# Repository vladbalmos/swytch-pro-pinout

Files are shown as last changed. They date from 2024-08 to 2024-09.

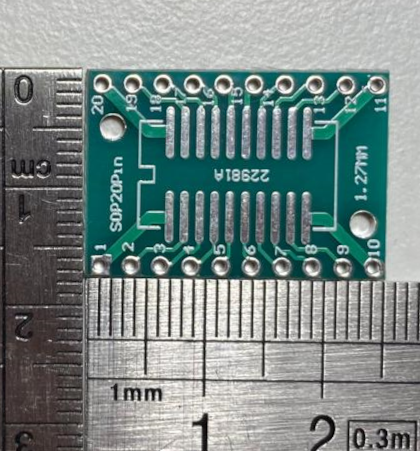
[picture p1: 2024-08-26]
junction-pcb.png

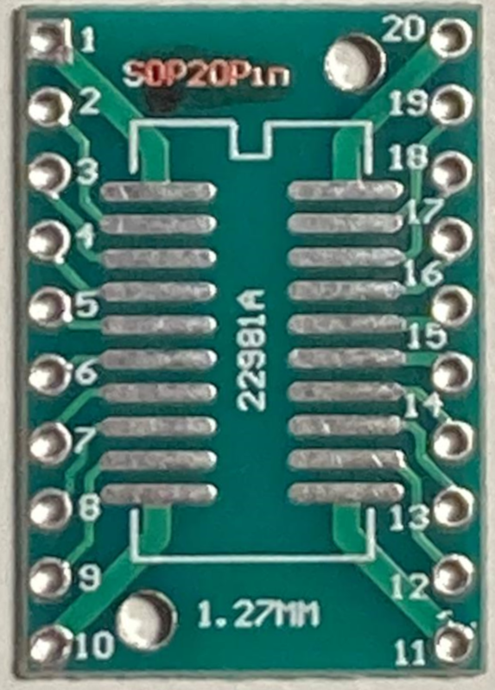
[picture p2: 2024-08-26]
junction-pcb-map.png

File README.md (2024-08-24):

# Swytch PRO Universal Kit (2nd Generation) pinout

The following is the pinout for the Swytch PRO Universal Kit (2nd Generation).

## Pinout for Quick Connect Handlerbar Mount

Front view, pin 1 is left most, pin 12 is right most.

| Pin Number | Description 
|---|---
| 1 | Motor temperature sensor signal 
| 2 | +5V rail 
| 3 | Motor HALL sensor signal 
| 4 | Motor HALL sensor signal 
| 5 | Motor HALL sensor signal
| 6 | Motor phase *
| 7 | Motor phase * 
| 8 | Motor phase * 
| 9 | Brake sensor signal 
| 10 | PAS sensor signal 
| 11 | Ground 
| 12 | Throttle sensor signal  

<small>
* - Not sure about the phase ordering
</small>

For the battery pack pinout just reverse the direction: pin 12 is left most while pin 1 is right most.

### Connectors pinout (handlebar mount)
The <strong>⮟</strong> character indicates the connector guide pin / keying feature. Pins identified with <strong>-1</strong> indicate <strong>No connection</strong>.

#### Motor (female - black)
Pin 8 is in line with the aligning arrow on the connector
<pre>
     ⮟
     8
  2     1
3   11   6
  5     4
     7
</pre>

| Pin Number | Description  
|---|---
| 8 | Motor phase * 
| 2 | +5V rail 
| 3 | Motor HALL sensor signal 
| 5 | Motor HALL sensor signal 
| 7 | Motor phase * 
| 4 | Motor HALL sensor signal 
| 6 | Motor phase * 
| 1 | Motor temperature sensor signal
| 11 | Ground 

<small>
* - Not sure about the phase ordering
</small>

#### Brake sensors (female - blue)

<pre>
    ⮟
-1     2
 9    11
</pre>

| Pin Number | Description  
|---|---
| -1 | Not connected
| 9 | Sensor signal
| 11 | Ground
| 2 | +5V rail

#### PAS sensor (female - orange)

<pre>
    ⮟
 2      10
    11   
</pre>

| Pin Number | Description  
|---|---
| 2 | +5V rail
| 11 | Ground
| 10 | Sensor signal

#### Throttle sensor (male - orange)

<pre>
    ⮟
 2      12
    11   
</pre>

| Pin Number | Description  
|---|---
| 2 | +5V rail
| 11 | Ground
| 12 | Sensor signal

### Voltages

| Pin Number | Description 
|---|---
| 1 | +3.3V
| 2 | +5V rail 
| 3 | +3.3V
| 4 | +3.3V
| 5 | +3.3V
| 6 | PWM 0 ... +48V
| 7 | PWM 0 ... +48V 
| 8 | PWM 0 ... +48V 
| 9 | +3V when unconnected, 0V when brakes engaged
| 10 | +3.3V
| 11 | Ground 
| 12 | 0 ... ~+4V, 0V when no throttle connected

## Connection map starting at the controller side and ending to the connectors out of the handlebar mount
See the [connector-map.png](./connector-map.png) for a visual guide. The pin numbering scheme is counter clockwise, pin 1 is left most starting from the connector keying feature

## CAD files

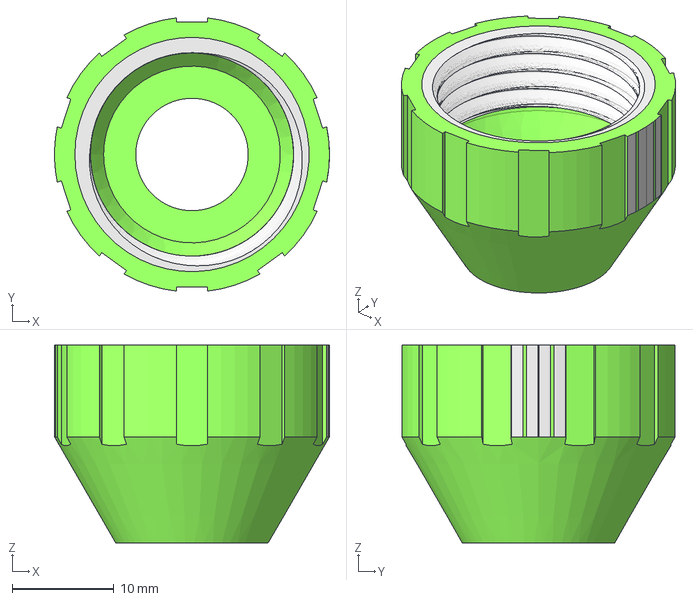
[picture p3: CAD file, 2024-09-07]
power-cable-connector-Housing_Female.step
27.0 x 26.8 x 19.4 mm
Body_Female_Thread
Body_Female

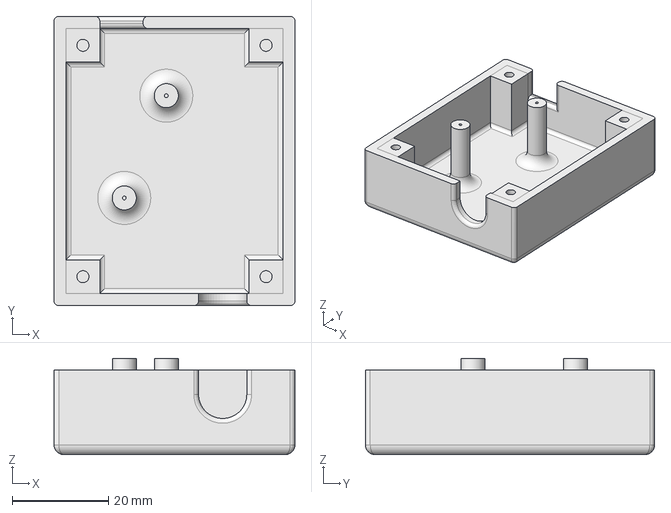
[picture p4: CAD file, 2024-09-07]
controller-wires-junction-box-Body_Box.step
50.0 x 60.0 x 19.9 mm

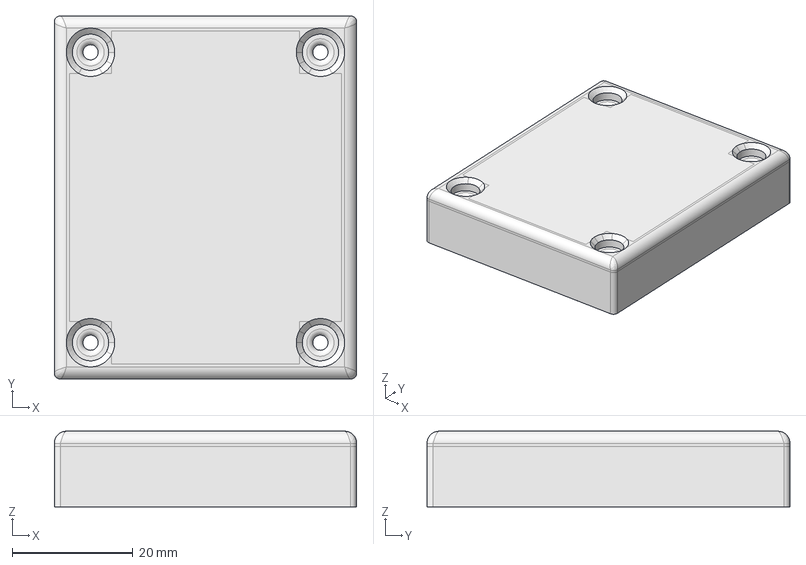
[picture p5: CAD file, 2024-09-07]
controller-wires-junction-box.FCStd
50.0 x 60.0 x 12.5 mm

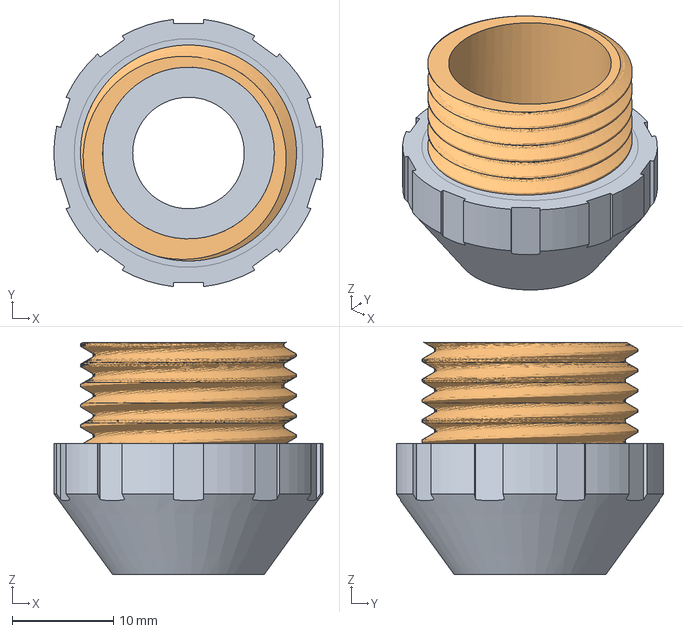
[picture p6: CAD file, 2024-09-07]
power-cable-connector-Housing_Male.step
26.6 x 26.5 x 23.0 mm
Body_Male
Body_Male_Thread

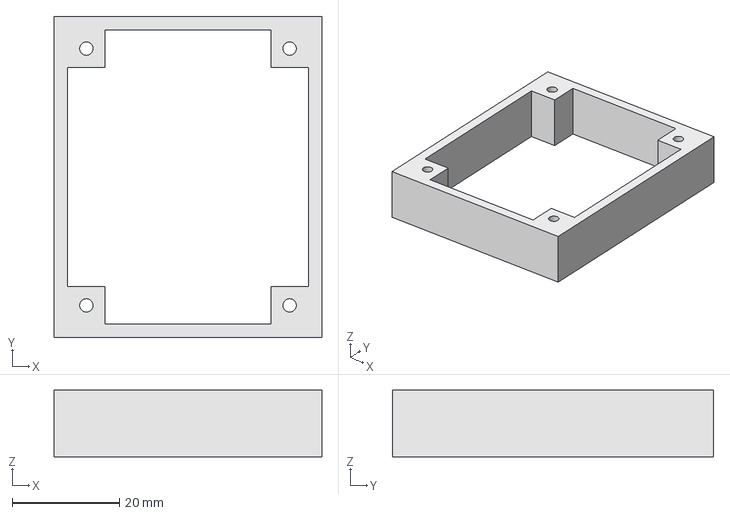
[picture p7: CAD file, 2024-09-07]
controller-wires-junction-box-Body_Wall.step
50.0 x 60.0 x 12.5 mm

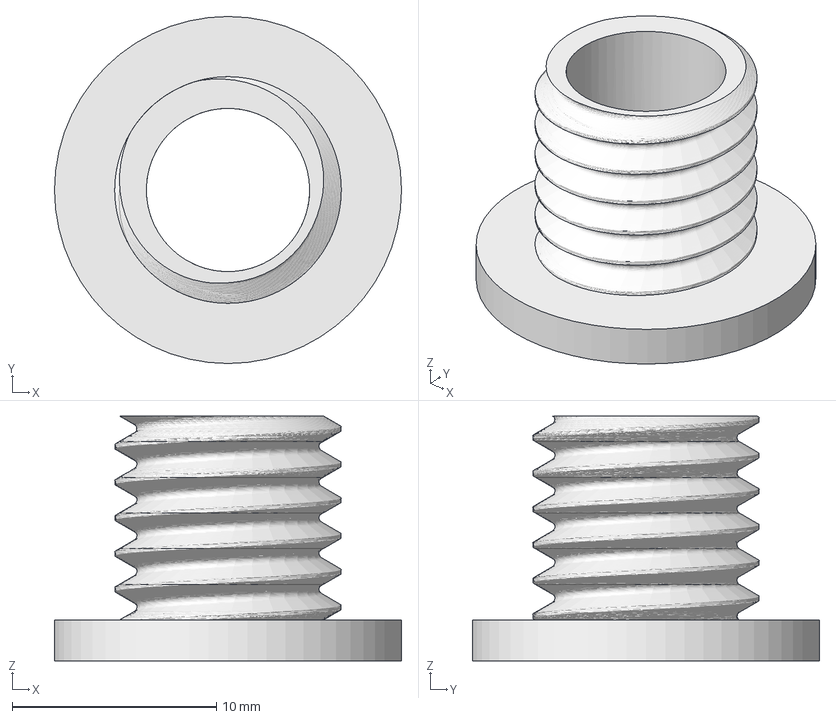
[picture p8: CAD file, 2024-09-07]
power-cable-connector-Cable_Gland_Body.step
17.0 x 17.0 x 12.0 mm

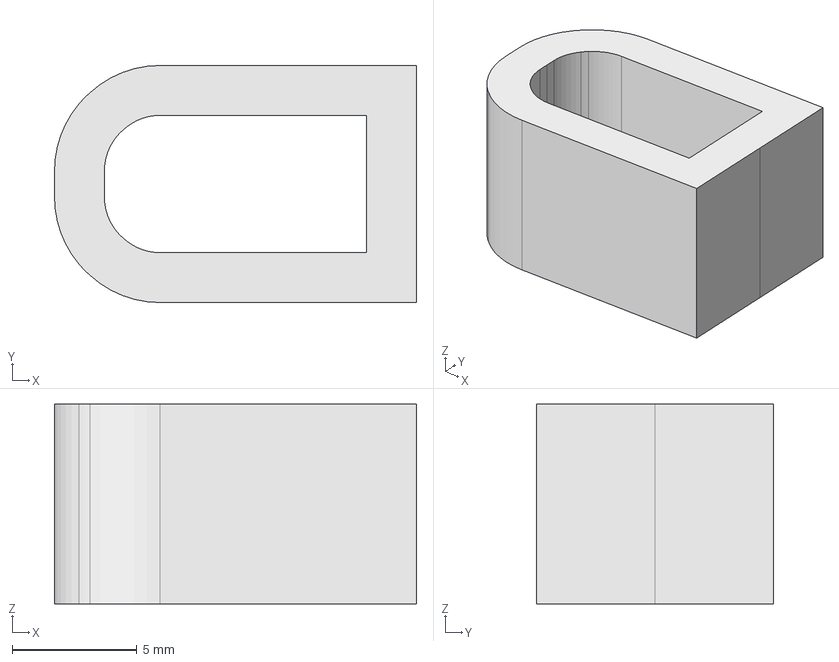
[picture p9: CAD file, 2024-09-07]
power-cable-connector-Body.step
14.5 x 9.50 x 8.00 mm

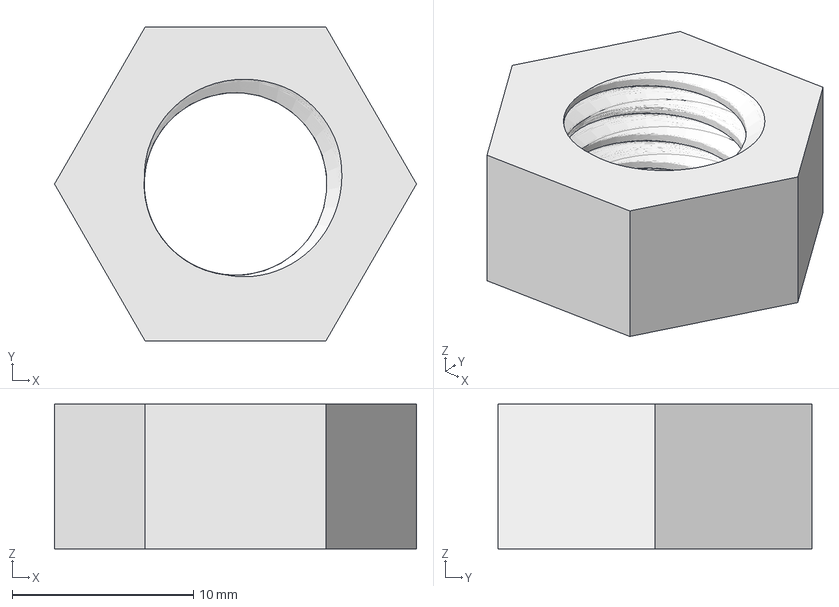
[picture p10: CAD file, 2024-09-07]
power-cable-connector-Cable_Gland_Nut.step
20.0 x 17.3 x 8.00 mm

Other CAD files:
controller-wires-junction-box-Body_Lid.step

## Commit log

2024-08-24 Reverse engineer wires
    [connector-wires.ods]
2024-08-29 Fix missmatched connection between PAS & Throttle
    [connector-wires.ods]
2024-09-07 Add final designs
    [controller-wires-junction-box-Body.step, controller-wires-junction-box-Body_Box.step, controller-wires-junction-box-Body_Lid.step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]
